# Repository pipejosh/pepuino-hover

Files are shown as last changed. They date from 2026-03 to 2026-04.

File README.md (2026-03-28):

# PEPUINO HOVER

This is a fully diy hovercraft, most of their parts are fully 3d printed, the only parts that are not is the foam chasi and the camping tarp bladder powered by a brushless motor, capable of hovering, and stearing. 

## Background 

Recently my friends wanted to start doing some RC stuff, we origninally wanted to do a drone, but the teacher gave us another challenge. Do a hovercraft, the idea was simple, he give us all the suplies, motor, esc, controller batteris and unlimited use of the school machines. The catch was, I had 1 month to do it, and if I was succesfull he would let us keep it. If we were not we had to sort all of the mixed up resistors he had in a box, so we accepted the challenge 

Turns out he would regreat this deal because the hovercraft would work flawlessly

(Note none of the parts on the render are the actual ones used, since I couldnt find the 3d models for them, they are there just just illustration effects + I didnt add the step of the prop since it is too big for github)

# Images

## Hovercraft Render
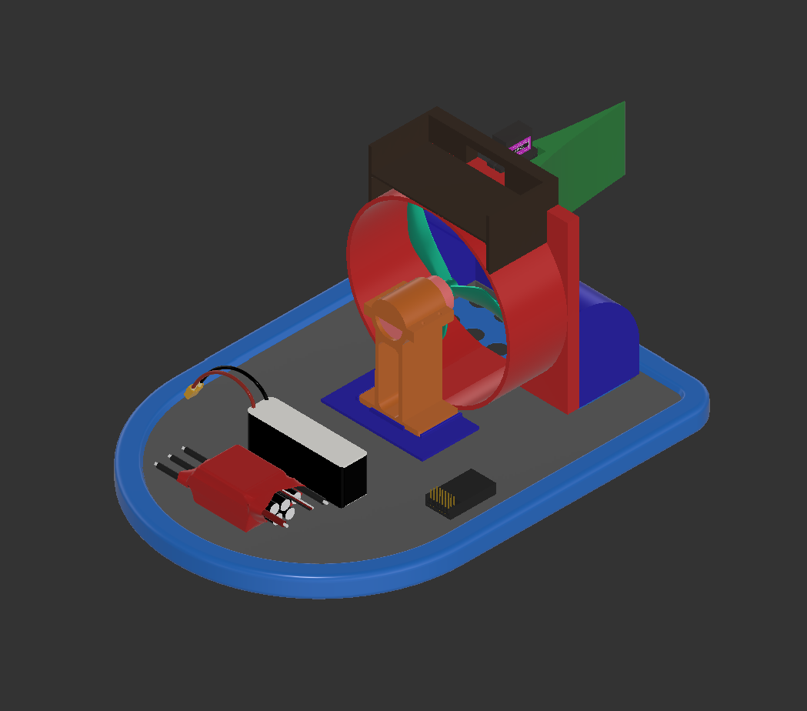
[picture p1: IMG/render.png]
duct
 

## Hovercraft Images
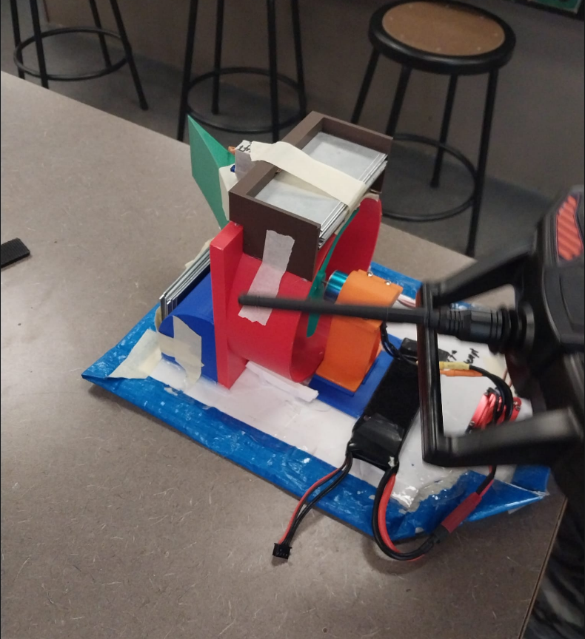
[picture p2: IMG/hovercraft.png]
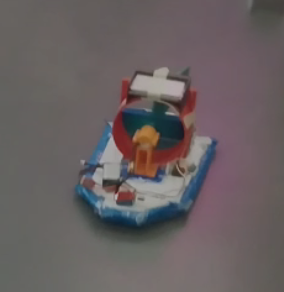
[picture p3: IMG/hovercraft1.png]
 

# Assembly Instructions
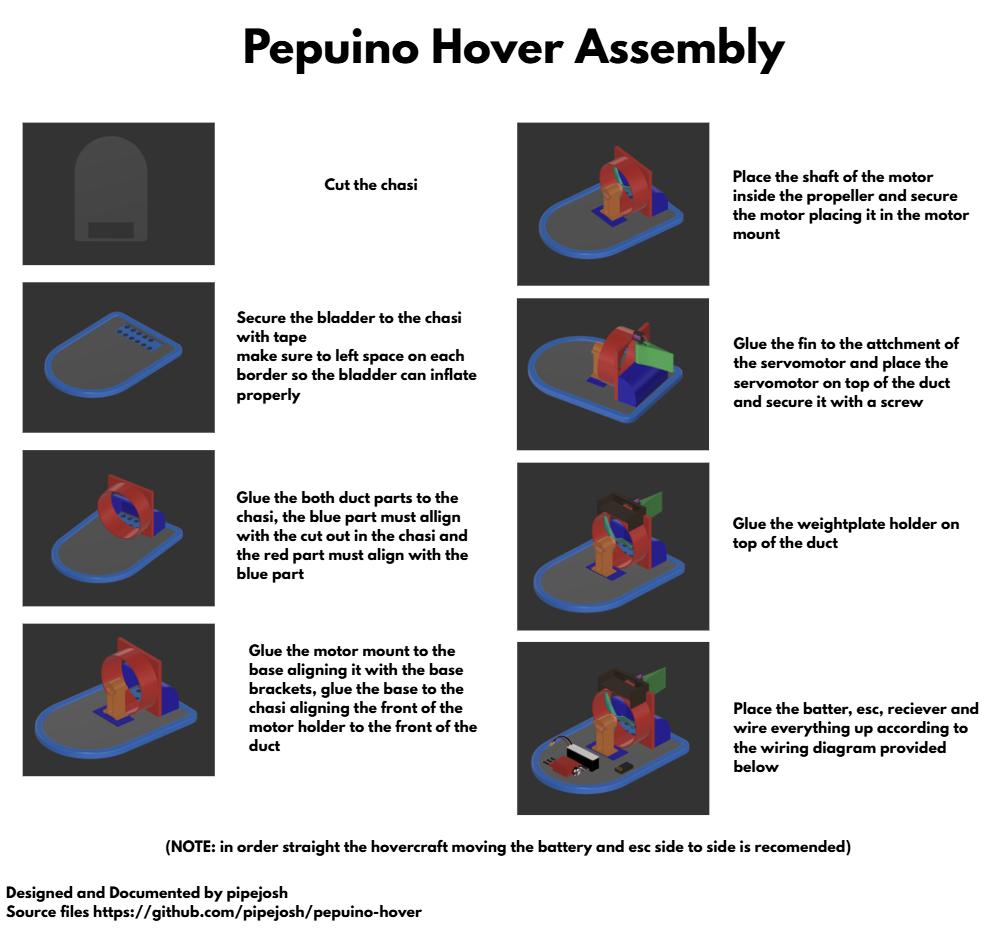
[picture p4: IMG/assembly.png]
assembly
 

## Wiring diagram
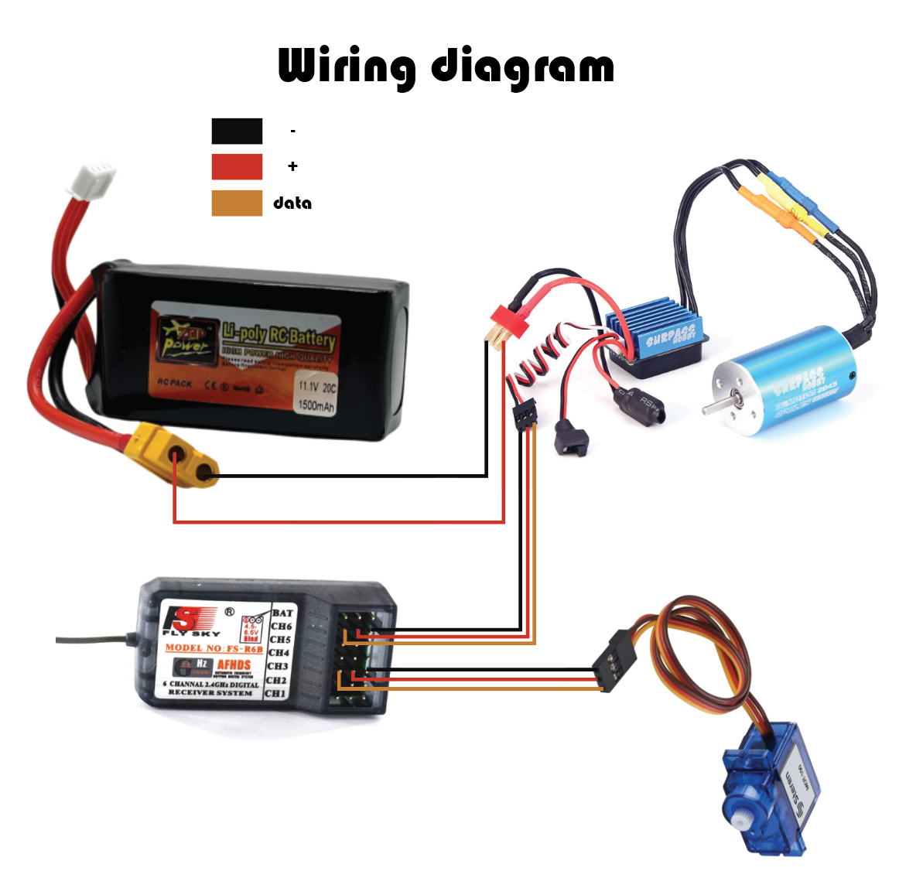
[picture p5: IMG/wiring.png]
wiring
 

# Video of the hovercraft

[Hovercraft video on Reddit](https://www.reddit.com/r/hovercraft/comments/1qpj7pu/our_very_colorfull_rc_hovercraft/)

# BOM

| KIT Items | Description | Quantity | Unit Price | Total Price | URL |
|---|---|---|---|---|-----|
| Motor + esc | surpass hobby shaft 2mm | 1 | 39,05 | 39,05 | https://www.aliexpress.com/item/1005007267459280.html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 |
| Controller + transmiter |  | 1 | 37,51 | 37,51 | https://www.aliexpress.com/item/1005010065941933.html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 |
| foam | this is used in the chase | 1 | 1,50 | 1,5 | https://dollarama.instacart.com/store/dollarama/products/28550706-foam-board-white-each |
| camping tarp | this is used in the bladder | 1 | 3,73 | 3,73 | https://www.aliexpress.com/item/1005005823228526.html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 |
| m3 scews | this is for the motor holder | 50 | 0,04 | 2,22 | https://www.aliexpress.com/item/1005005070119421.html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 |
| aliexpress tax |  |  |  | 5,00 |  |
| **Total** |  |  |  | **89,01** |  |

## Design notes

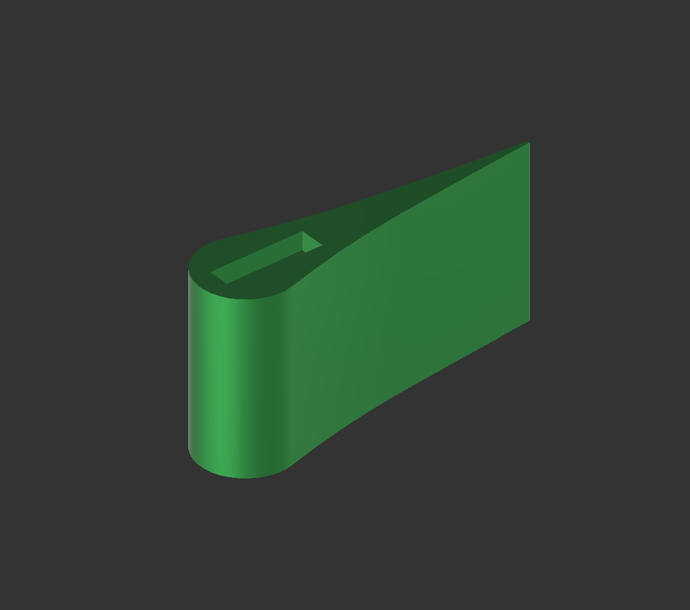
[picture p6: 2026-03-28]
IMG/fin.png

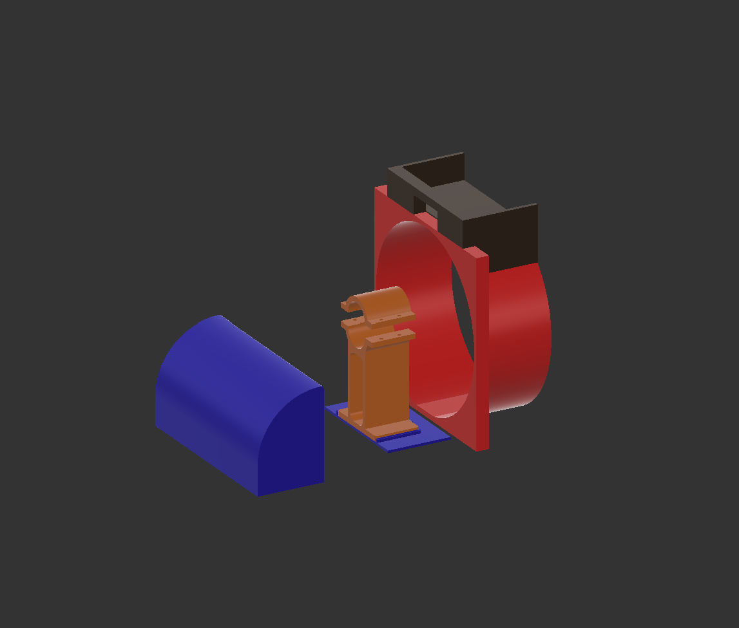
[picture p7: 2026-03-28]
IMG/duct.png

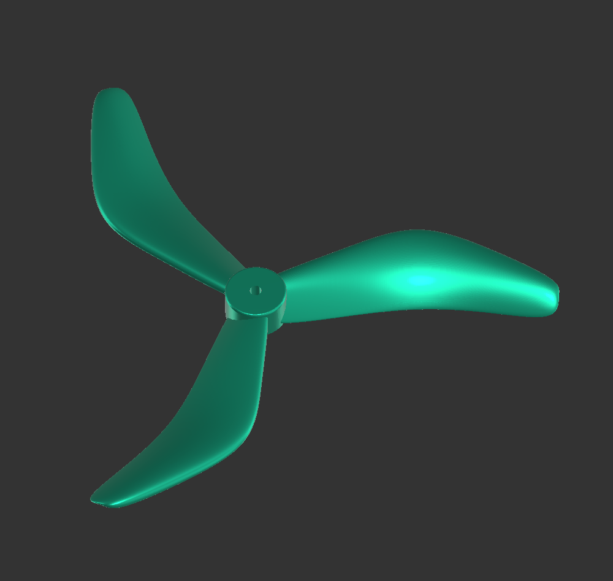
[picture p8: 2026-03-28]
IMG/prop.png

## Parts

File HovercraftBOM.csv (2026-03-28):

KIT Items | Description | Quantity | Unit Price | Total Price | URL
Motor + esc | the brand i use is surpass hobby | 1 | 39,05 | 39,05 | https://www.aliexpress.com/item/1005007267459280.html
Controller + transmiter |  | 1 | 37,51 | 37,51 | https://www.aliexpress.com/item/1005010065941933.html
foam | this is used in the chassis | 1 | 1,50 | 1,5 | https://dollarama.instacart.com/store/dollarama/products/28550706-foam-board-white-each
camping tarp | this is used in the bladder | 1 | 3,73 | 3,73 | https://www.aliexpress.com/item/1005005823228526.html
m3 scews | this is for the motor holder | 50 | 0,04 | 2,22 | https://www.aliexpress.com/item/1005005070119421.html
aliexpress tax |  |  |  | 5,00
 |  |  | Total | 89,01

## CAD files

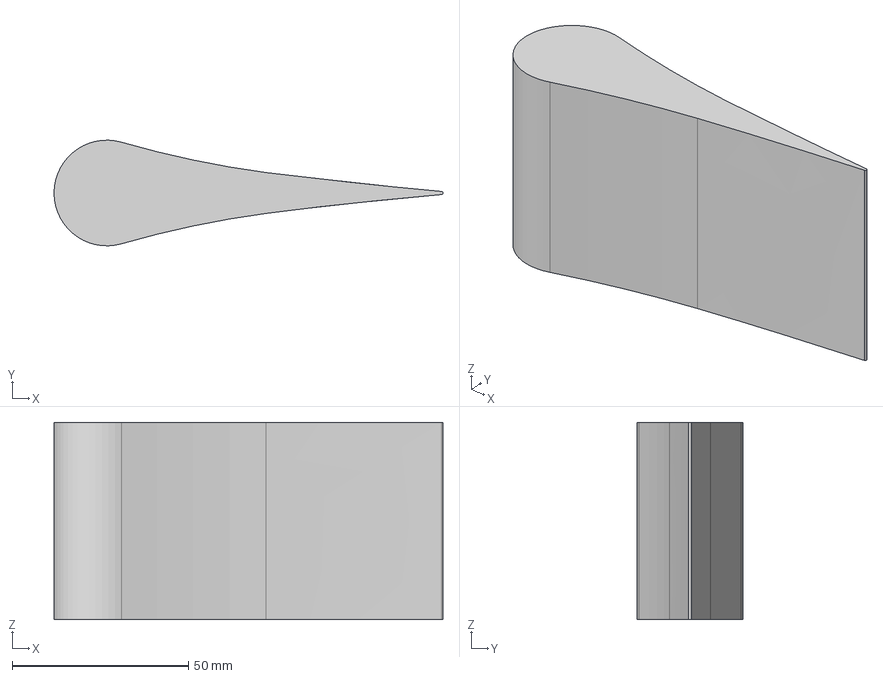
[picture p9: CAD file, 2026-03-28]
CAD/3D/Finn McMissle.step
110.4 x 30.0 x 56.0 mm

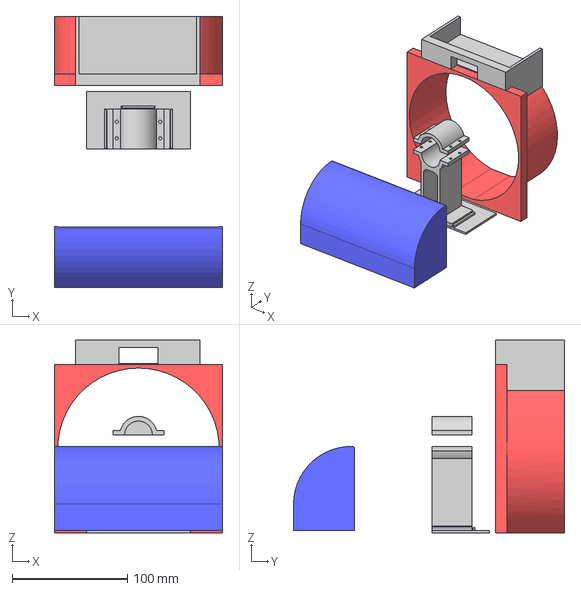
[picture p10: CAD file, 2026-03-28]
CAD/3D/Duct + motor stand + weightplate holder.step
146.0 x 235.0 x 167.3 mm

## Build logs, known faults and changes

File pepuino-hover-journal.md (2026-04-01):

<!--
  This journal is auto generated by Hack Club Blueprint.
-->

# 12/11/2025 - Design and cut the chasi and bladder  

_Time spent: 2.0h_  

This is my second time doing a hovercraft, the school provides the machines, materials and all I need, so I dont need any funding.

The first part of this journey starting designing the chasi, and therefore the bladder, the foam we are using is the one from dolarama (2 bucks a sheet of foam) and its 2cm thick, sou after some very "constructive" conversation with my teamater (they wanted to do a gearbox and a cluch mechanism" the chasi and the bladder were designed! and after a bit of time we had them cutted in the laser machine too! the blader is made out of camping tarp a light material that our teacher bought a lot last season so thats why we are using it

bladder prototype


Chasi prototype



# 12/12/2025 - Cutted the chasi and bladder + desing and print the duct  

_Time spent: 6.0h_  

Today was such a fun day, because I got to use the laser machine at my school, I cutted the foam, and the bladder made out of camping tarp, the laser process was easy but tedious (it took a bit of time) to do all that.

And once that was cutted, I joined then with one of the most strong glues in the entire universe, tape, so once together we that the holes in the bladder were way to big, so 30 minutes later, and another trip to the laser machine, bladder V2 was ready (and it looks awesome)

And to end the day, I started designing the duct, in order to get more drag therefore making it better, this is just V1 of the design, so it might get updated, and 3 hours later, it was printed and ready to be assembled

Duct printed V1
Imagen de WhatsApp 2025-12-12 a las 17.26.39_205d78bc

Bladder and chasi assembled
Imagen de WhatsApp 2025-12-12 a las 17.26.58_67d59532

Chasi and esc
Imagen de WhatsApp 2025-12-12 a las 17.26.58_822ffc33

# 12/14/2025 - Redesigning the duct  

_Time spent: 4.0h_  

Weeeeeell turns out that the previous version of the duct was way to short, the motor didnt fit inside it, so its fine for version 2 of the duct, which is gonna align with the hole for the air to flow and its gonna be awesome, so 2 hours later and some "problems" (we didn't know which color we wanted the duct to be) duct V2 was exported sliced and printed in my friends bambu lab a1 mini!

the final color was red for the duct, and blue for the air chamber that conects

render 




# 12/15/2025 - design the mount for the motor + design props  

_Time spent: 4.5h_  

Todays work was just designing stuffff, back at my house with my computer that actually can handle fusion 360, i spend 3 to 4 hours designing the motor mount, it's a relative simple design that took ages to bring the concept to life, I figured I wanted the motor to be easy removed from the stand, so with the measure of some m3 screws and some music the mount was doneeeee, that was just pt1 of the day, since the other part went to making the prop, i reused the model that i did for a drone prop a while ago, just imported the stl, and changed the size of the hole to make it fit the shaft of this new motor, after some trial and error, and some wrong measuremnts the prop was done too

prop


motor stand


# 1/28/2026 10:37 AM - First testing! + retaping the blader  + primitive stearing  

_Time spent: 3.0h_  

after mounting every component togethr (esc, motor, batery, transmitter) and putting the hardware together, it was time for the first testing, the first testing, went gud just that, the hovercraft, was not hovering, so that was a problem, and turns out i didnt leave any space in the blader so i can inflate, so after a tediuos 30 minutes removing the tape, i measured it correctly this time making sure it was centered, and once we thought war was over, we still wanted to add a primite stearing before calling it a day, so we grabbed a piece of foam, and tape it to the servo, that was previously taped to the top of the duct (everything in this proyect is yanky hehe)

picturessss of how the hovercraft is goinggg




# 1/28/2026 10:52 AM - Design Finn McMissile + print it + asseble it  

_Time spent: 2.0h_  

Weeell u guys remember how in the previos jornal i talked about how our primitive stearing, weell turns out if its absolute sh*t, so, they made me design (because im the only one that knows how to use fusion) a fin for the hovercraft, what we thinking was something slim, that would allow air to start strong, and end up at the end very compressed, and after talking to the physics teacher, and about 2 hours rant later, about aerodynamics, we sketch in a paper the idea for the fin, and it was just a matter of time untill i could fully designed it in fusion 360, and after the design process was done, the hardest part arrived, what should we name it????? weeeeeeeeeeeeeell the answer was obious FINNNNN MC MIISIILEEEE (the electronics teacher hated the name) 

It was time to print it, i knew that the piece needed to the as light as possible, so for my needs i use 5 percent lightning infill, and honestly i thought the print was gonna fail, because hooooly is was hollow, but my centauri carbon handled it like a champ.

And after the printing was done, we just mounted it to the hovercraft, gluing it with hot glue to the servo and taping plus hot gluing the servo to the top of the duct.





finnn mcmissiiileeee has succesfully been assembleddd!!!

# 1/28/2026 11:05 AM - Problems start arriving  

_Time spent: 1.5h_  

SO once we thought the hovercraft was reeady, ready for everything, turns out it wasnt, the freaking bladder was uneven at the ends, since the design of the chasi was a rectangle with a circular edge, it was really difficult to tape the bladder pecisely on both sides, so this is the point where out hero, lets call him Sam, arrived, Sam was also doing his hovercraft, and i noticed he has a really really nice taped blader, so i asked him if he could give us a hand with the taping proces that we were strugling, and so he did the new taping was perfect, everything symetrical we test it and in fact, it was perfect, perfect until my friend (thats was driving the hovercraft) decided it would be a gud idea to crash the hovercraft, and the prop broke, so we replace it, and by mistake we place it in the other direction, and to our surprise, what we thought was a mmistake, turned out being the most important thing of out whole proyect, the hovercraft suddenly became more powerful, more fact, and therefore more uncontrolable, but thats a problem we will solve later

this is a close up the image in the journal entry below, this is SAMS prisitne taping


# 1/28/2026 11:17 AM - Trying weight plates + FIRST CRASHHH!  

_Time spent: 2.5h_  

since the hovercraft wasvery fast and uncontrolable, we as a team decided to add weeeeightplateeeeess so the hovercraft could be easier to drive, so the teacher gave us a sheet of aluminum and told us "cut it to your deside" so we ended up cutting little squares of 8 by 5 ishhhh we cutted 35 hehe, our first instict was to tape it to the top of the duct exactly where the servo is, so we went ahead and do that, test it, and ...

PUM CRASH all the weightplates fly away from its intended spot the prop gave up and decided to end it all, chipping the top of the duct, the motor stand that was supposed to hold the motor in place decided to let go to is was so bad even the foam that was glued to the motor was ripped out of the chasi (u can tell it is dollarama stuff), EVERYTHING WAS BROKEN, everything but our faith in the proyect (this proyect is worth 30 percent of out electronics mark)



# 1/28/2026 11:26 AM - redesign the motor mount + thing so the weightplates can sit  

_Time spent: 3.0h_  

after the fatal crash yesterday, i went ahead and design a little plate for the motor, so there is more contact surface and the glue actually works, plus a little rack for the weightplates to sit on, this one was the easy part, since i worked with the duct i had already designed

And after a bit of effort, time and prayers (my friend decided to print the weightplate thing in his ender 3 so we did a little prayer before the print started so it could go through) the thing was doneeeee, and then in the spot we decide to test in again once the prop was changed, the motor was glued and the thing to hold the weightplates was asasebled and we changed FINNNN MCMISILEEEE because it also suffered from damage from the crash







# 1/28/2026 11:39 AM - Another crashhh  

_Time spent: 2.0h_  

One day before the proyect was due, all looked in shape, bladder inflating correctly stearing was hard but achievable, propeller strong, and overall it worked, so we diceided to just get used to the controllers, not do anything STUPID, and then second after i said that, i head a big PAMMMMM, they had crash it again

this one was less severe than the othe onee just because the propeller didnt blow up this time, but the motor stand did so after some hot hot glue, and superglue and every type of glue known to mankind, it was up and ready to go, the chasi internally was broken in half, but we didnt have time to cut the chasi again, because the proyect was due the next day, so we just add more foam that would act as a support, more glue and called it a day

 

# 1/28/2026 12:12 PM - The testing day!   

_Time spent: 3.0h_  

Today was the day, everything would be defined, the day our hovercraft would be jusged by the teacaher, and in base of his opinion it was decided if we fail or not the course, so with full trust of our blood sweat and tears, we have the controler to the most expericned out of all (thats the friend that crashed twice into the wall) and surprisingly WE MADE IT we passed the circuit the teacher had made, ofc we didnt ran it full power because we needed precision over speed, and after we consolidated our victory i took a video on how the hovercraft worked!! one of the most demaning proyects ive worked on was finally completed!!!!!!!



 [WhatsApp Video 2026-01-28 at 11.30.26](/user-attachments/blobs/proxy/eyJfcmFpbHMiOnsiZGF0YSI6OTQwNzEsInB1ciI6ImJsb2JfaWQifX0=--f084542fb150567d9dc07cb03a334ba55cf120b7/WhatsApp%20Video%202026-01-28%20at%2011.30.26.mp4)

# 1/28/2026 12:18 PM - Linked the repo  

_Time spent: 0.1h_  

For the review, i forgot to linked the repo and i already submited it here is the repo link thank u for your undertanding

https://github.com/pipejosh/hovercraft



# 2/3/2026 - set up the repo!  

_Time spent: 1.5h_  

last time i submited i forgot to link the github repo, so now i set it up plus i made it prettyyy i add the pictures and the reddit post linked to the video of the hovercraft working



# 3/28/2026 - housekeeping  

_Time spent: 1.5h_  

today was organizing the repo mostly tweaking the images, sorting all into folders and overall making it look better.

Beside this I also created the assembly instruciton in canva.



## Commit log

2026-03-28 update picutes and add assembly picture
2026-03-28 Revise README with assembly instructions and BOM updates
    Updated the README to include assembly instructions and corrected some descriptions in the BOM.
2026-03-28 update the render and sort everything in folder
    [Duct + motor stand + weightplate holder.step, Finn McMissle.step]
2026-03-28 Update URLs and prices in Hovercraft BOM
    [HovercraftBOM.csv]
